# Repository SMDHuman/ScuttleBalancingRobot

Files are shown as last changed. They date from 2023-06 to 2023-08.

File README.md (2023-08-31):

# Scuttle Self-Balancing robot

This project of mine was built with the support of [SCUTTLE™](https://www.scuttlerobot.org/). 

## About The Project

This project's subject is to make SCUTTLE Robot balance itself on its two wheels only modifying its default shape and use external MPU6050 sensor in addition. Main idea of this project comes from David Malawey who is Founder of The Scuttle™ and I am glad to bring this idea to reality. Before working on this project i had one project similar to this and it's called [LOTP_BalanceWheel](https://github.com/SMDHuman/BalanceWheel) and its purpose is to make a 3D printed frame, stepper motor driven and Raspberry Pi Pico based two wheels self-balancing robot.

However I have built a two wheels self-balancing robot before, there were a few challenges on this project which I enjoyed a lot. Scuttle Robot has already a predefined setup and I was limited to transform current model in a most easiest and efficient way. Also a new part was designed and printed for this project to be able to hold MPU6050 sensor on the chassis.

Final result is a milestone and an evolutionary progress at SCUTTLE development for all community.
SCUTTLE Robot is designed very efficiently and maker friendly.  Standard form is a very good start for different purpose designs. It may be adapted for various potential tasks. There are still many challenges hidden at SCUTTLE Robot for curious makers. This project is a very good sample of that. I hope you enjoy while you are building your own.

## Requirements 

If you want to replicate this project on your own, you'll need;
1.	Raspberry Pi Computer,
2. [Scuttle Robot Base Parts](https://github.com/SMDHuman/ScuttleBalancingRobot/blob/main/docs/Item%20Links%2020230606.pdf),
3.	MPU6050
4.	Custom 3D Printed Parts,
5.	Basic Python Knowledge,
6.	Basic understanding of PID Controller (in case of re-tuning PID)

With all of those you can easily remake or iterate on top of it.

# Getting Started

First of all you need the robot itself to install and run the programs. If you have one, then you are lucky! You just need to transform the shape of the robot and attach external MPU6050 sensor and a [3D print part](https://github.com/SMDHuman/ScuttleBalancingRobot/tree/main/3D%20Models) to mount it. You can start this process by looking up my step by step [YouTube](https://youtu.be/XI1HBQYeNek) guide with English subtitle or check out the [PDF](https://github.com/SMDHuman/ScuttleBalancingRobot/blob/main/docs/Self%20Balanced%20Robot%20Transformation.pdf) of the transformation of the robot from base model to self-balancing configuration.

If you don't have the robot, then you can obtain all the parts from [Scuttle Shop](https://www.scuttlerobot.org/shop/) or from your local shops. You can look the parts and specification of those parts from this [PDF](https://github.com/SMDHuman/ScuttleBalancingRobot/blob/main/docs/Item%20Links%2020230606.pdf) or in that [Link](https://www.scuttlerobot.org/resources/). You will find lots of documentation about SCUTTLE Robot in this link too.

## Wiring of Necessary Components

You have to wire all electrical components to each other that are in use of our project. We need to wire
*	Batteries to Regulator,
*	Batteries to Motor driver,
*	Regulator to Raspberry Pi,
*	Raspberry Pi to Motor Drivers,
*	Motor Driver to DC Motors,
*	MPU6050 to Raspberry Pi.

You can check out the connections of all parts and more from this Link except MPU6050. MPU6050 needs to connect to Raspberry Pi as the picture shows under below.

Direct Connections with Raspberry Pi and MPU6050

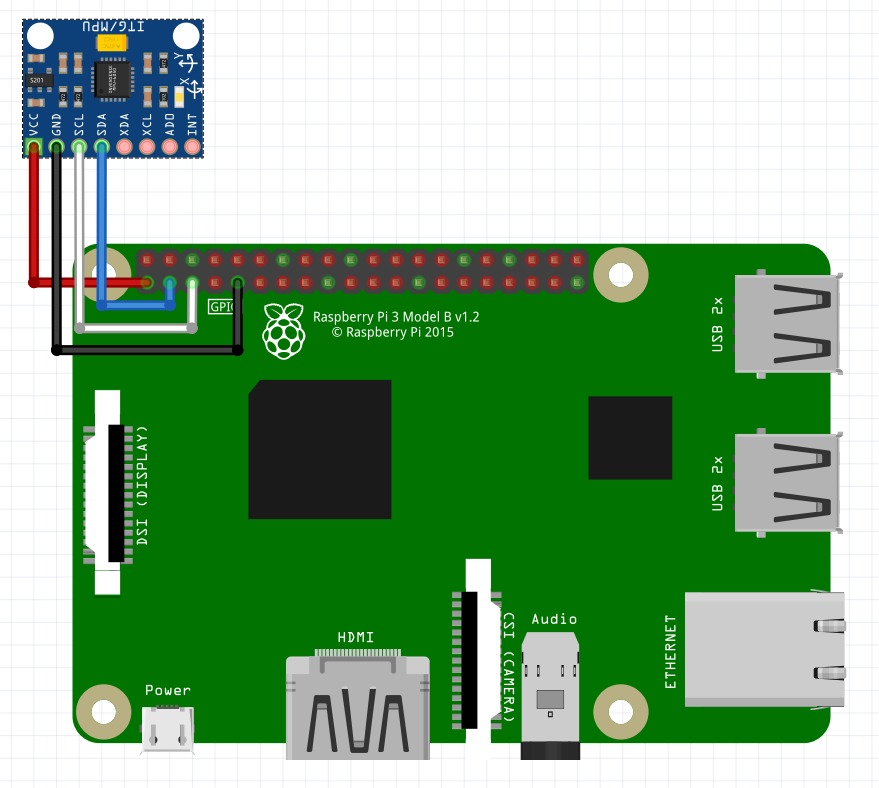
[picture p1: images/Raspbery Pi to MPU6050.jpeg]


Connection Via I2C Breakout Board

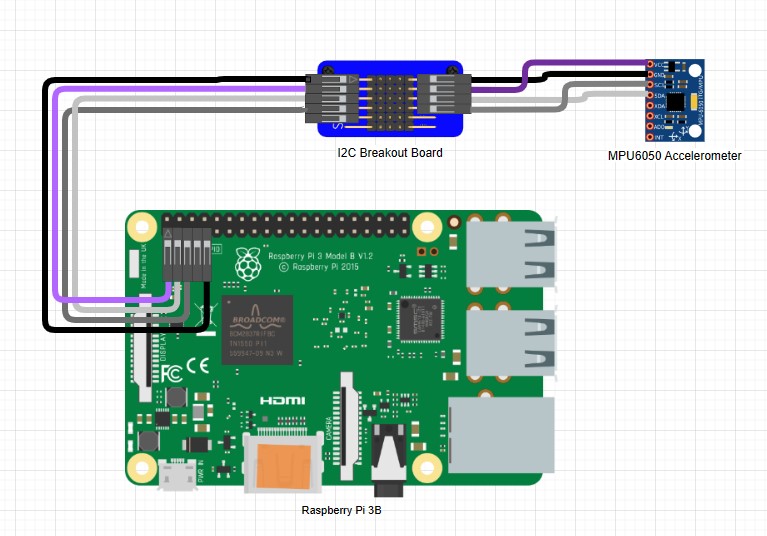
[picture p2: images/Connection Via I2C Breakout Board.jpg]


If you can't see the picture, here is a table of the wiring of the pins between MPU6050 and Raspberry Pi. You may also access the diagram designed on [Draw.io](https://drive.google.com/file/d/1K8wL2eJak03yuCxYKJeCcMRbwO4yd8io/view?usp=sharing)

| MPU6050 | Raspberry Pi |
|---|---|
| VCC | 3.3V |
| GND | GND |
| SCL | GPIO 3 |
| SDA | GPIO 2 |

## Installation 
You can follow the step by step guide from [this document](https://github.com/SMDHuman/ScuttleBalancingRobot/blob/main/docs/Software%20Installation%20Guide%20v1.pdf) prepeared for installation of OS and running the python code for self balancing scuttle robot.

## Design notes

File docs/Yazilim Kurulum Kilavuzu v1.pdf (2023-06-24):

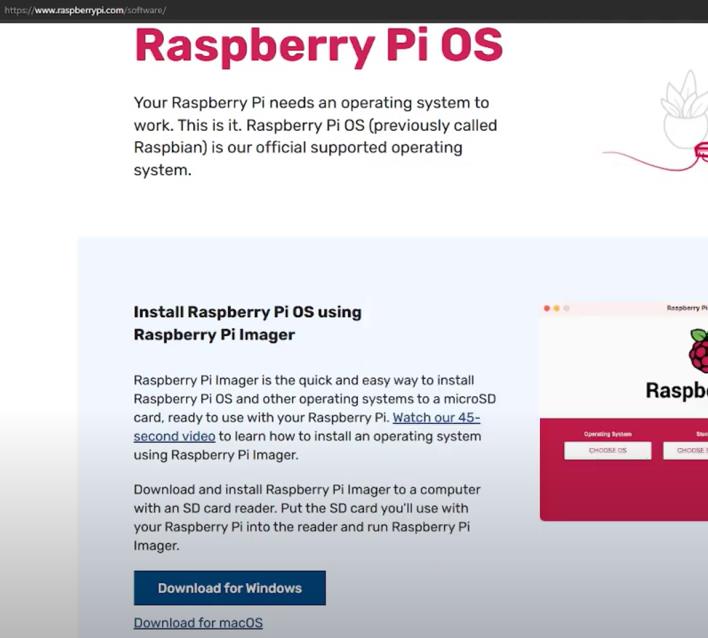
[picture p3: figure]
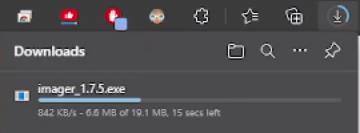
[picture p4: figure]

SCUTTLE Denge Robotu - Yazılım Kurulum Kılavuzu | Dok Ver. 1.0

Sayfa

1

## SCUTTLE Denge Robotu - Yazılım Kurulum Kılavuzu

### 1. Adım : Raspberry Pi’nin SD kartını Bilgisayarımıza takıyoruz

Minimum 4 GB bir SD kart yeterli olacaktır.

2. Adım : Rasberry Pi’nin web sitesinden Raspbian işletim sisteminin Lite versiyonunu indirip Raspberry Pi’nin SD kartına kurulumunu yapıyoruz, gerekli seçenekleri ve bilgileri giriyoruz.
a. İlk olarak Rasberry Pi’nin web sitesini açıyoruz ve “software”i seçiyoruz.

https://www.raspberrypi.com/software/

b. Bu bölümden Raspberry Pi Imager programını indiriyoruz.

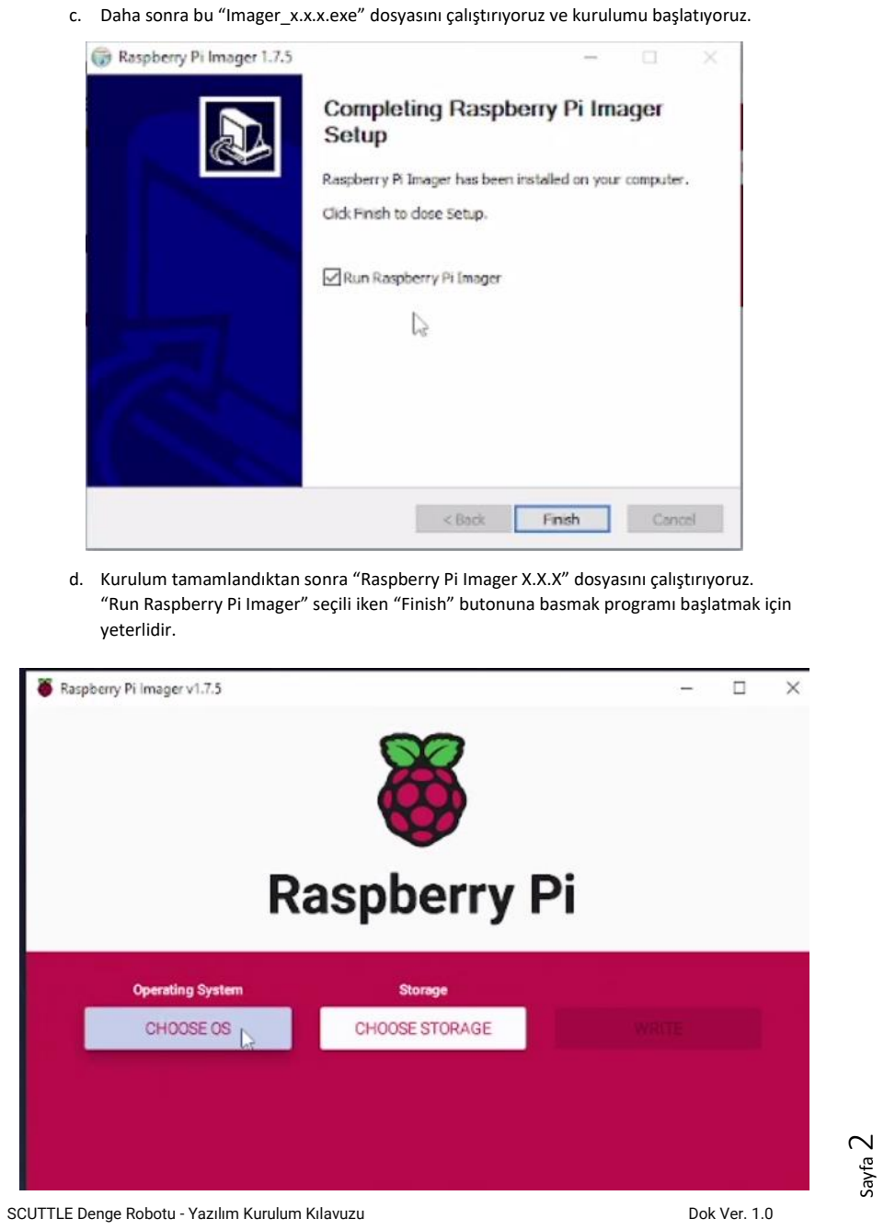
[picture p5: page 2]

Sayfa

2

c. Daha sonra bu “Imager_x.x.x.exe” dosyasını çalıştırıyoruz ve kurulumu başlatıyoruz.
d. Kurulum tamamlandıktan sonra “Raspberry Pi Imager X.X.X” dosyasını çalıştırıyoruz. “Run Raspberry Pi Imager” seçili iken “Finish” butonuna basmak programı başlatmak için yeterlidir.

Sayfa

3

e. İlk olarak “Choose OS” butonuna basarak işletim sistemini seçeceğimiz pencereyi açıyoruz. Burada önce “ Raspberry Pi OS (other)” seçeneğini seçiyoruz.
f. Daha sonra “Raspberry Pi OS Lite (32-bit)” işletim sistemini seçiyoruz. Siz dilerseniz “Raspberry Pi OS (32-bit)” işletim sistemini de seçebilirsiniz.
g. Ardından işletim sisteminin nereye kurulacağını seçmek için “Choose Storage” butonuna basıyoruz.
h. SD kartımızı seçiyoruz.

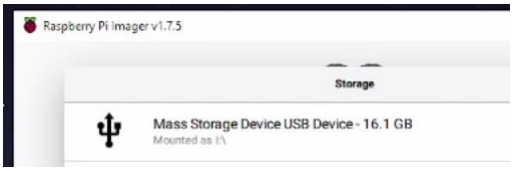
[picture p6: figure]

i. Diğer işleme geçiyoruz ve “Ayarlar” butonuna basıyoruz.
j. Açılan pencerede ilk olarak “image customization options” için “to always use” seçeneğini seçiyoruz. Böylece bu yaptığımız ayarları her seferinde yeniden yapmamıza gerek kalmıyor ve bu değişiklikler kalıcı şekilde sisteme kaydediliyor.

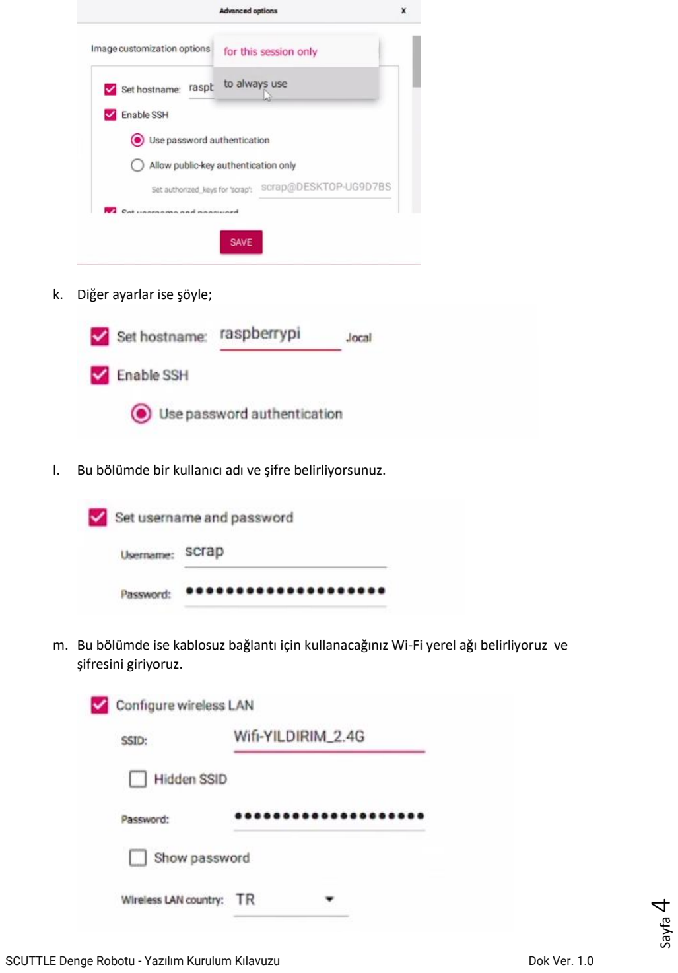
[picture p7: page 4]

Sayfa

4

k. Diğer ayarlar ise şöyle;
l. Bu bölümde bir kullanıcı adı ve şifre belirliyorsunuz.
m. Bu bölümde ise kablosuz bağlantı için kullanacağınız Wi-Fi yerel ağı belirliyoruz ve şifresini giriyoruz.

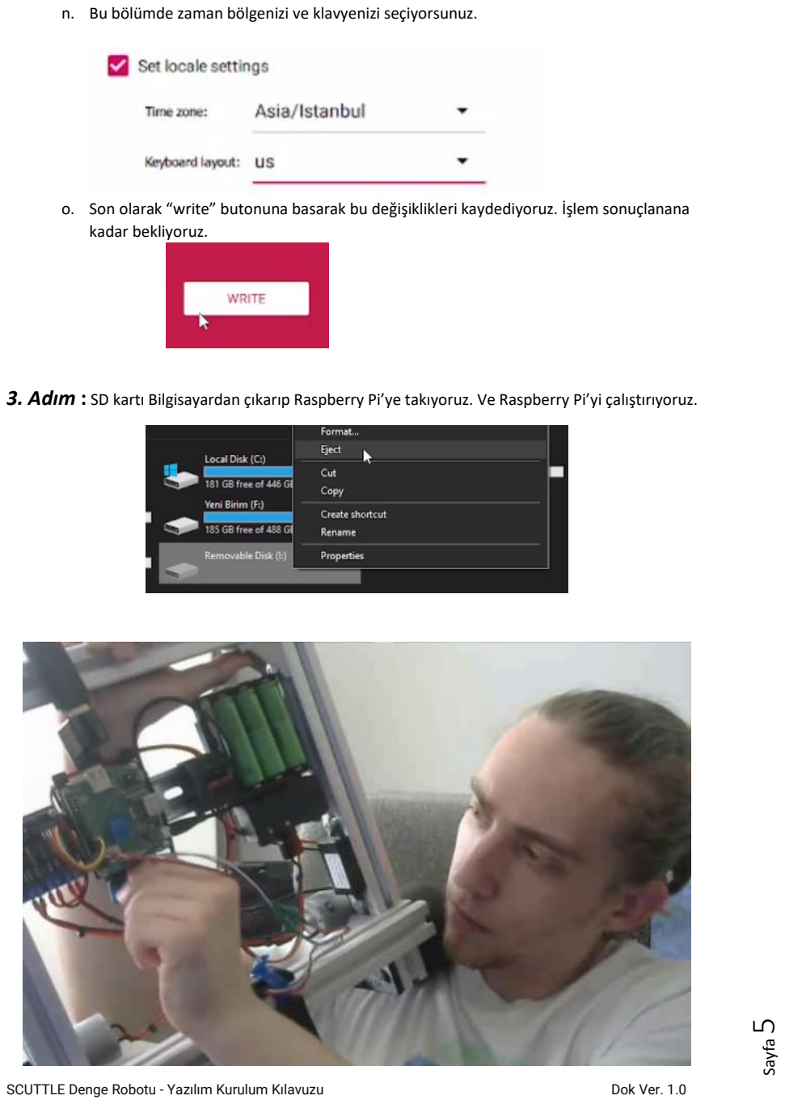
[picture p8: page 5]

Sayfa

5

n. Bu bölümde zaman bölgenizi ve klavyenizi seçiyorsunuz.
o. Son olarak “write” butonuna basarak bu değişiklikleri kaydediyoruz. İşlem sonuçlanana kadar bekliyoruz.
3. Adım : SD kartı Bilgisayardan çıkarıp Raspberry Pi’ye takıyoruz. Ve Raspberry Pi’yi çalıştırıyoruz.

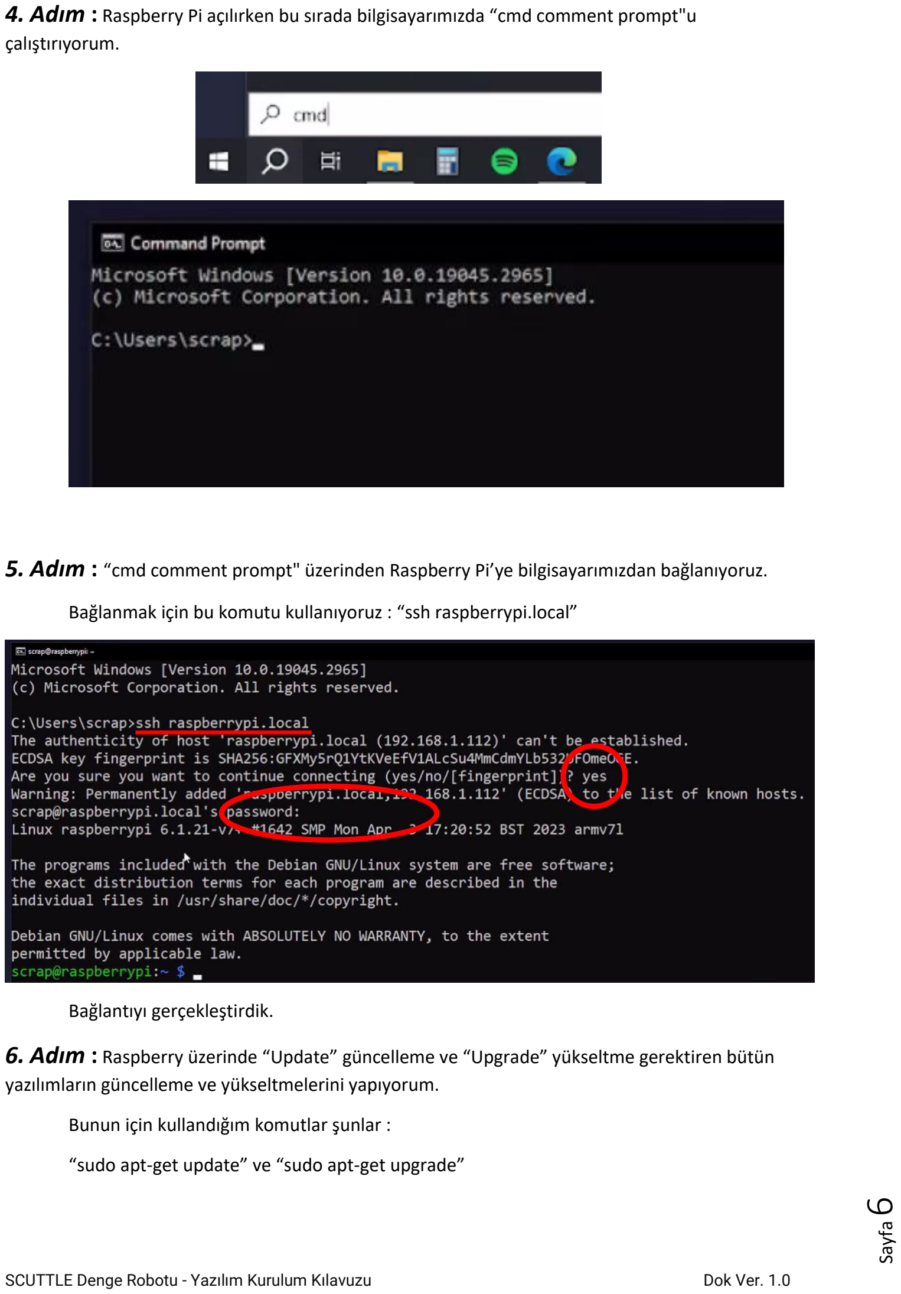
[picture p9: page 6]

Sayfa

6

### 4. Adım : Raspberry Pi açılırken bu sırada bilgisayarımızda “cmd comment prompt"u

çalıştırıyorum.

5. Adım : “cmd comment prompt" üzerinden Raspberry Pi’ye bilgisayarımızdan bağlanıyoruz.

Bağlanmak için bu komutu kullanıyoruz : “ssh raspberrypi.local”

Bağlantıyı gerçekleştirdik.

### 6. Adım : Raspberry üzerinde “Update” güncelleme ve “Upgrade” yükseltme gerektiren bütün

yazılımların güncelleme ve yükseltmelerini yapıyorum.

Bunun için kullandığım komutlar şunlar :

“sudo apt-get update” ve “sudo apt-get upgrade”

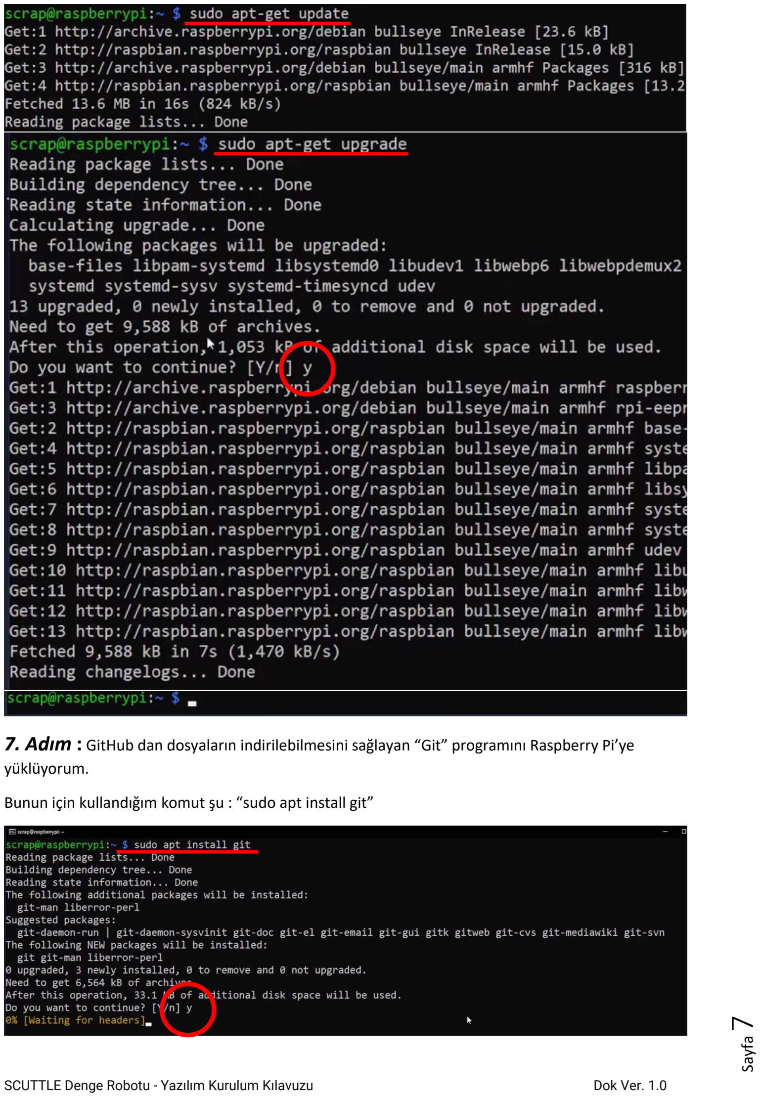
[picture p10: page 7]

Sayfa

7

7. Adım : GitHub dan dosyaların indirilebilmesini sağlayan “Git” programını Raspberry Pi’ye yüklüyorum.

Bunun için kullandığım komut şu : “sudo apt install git”

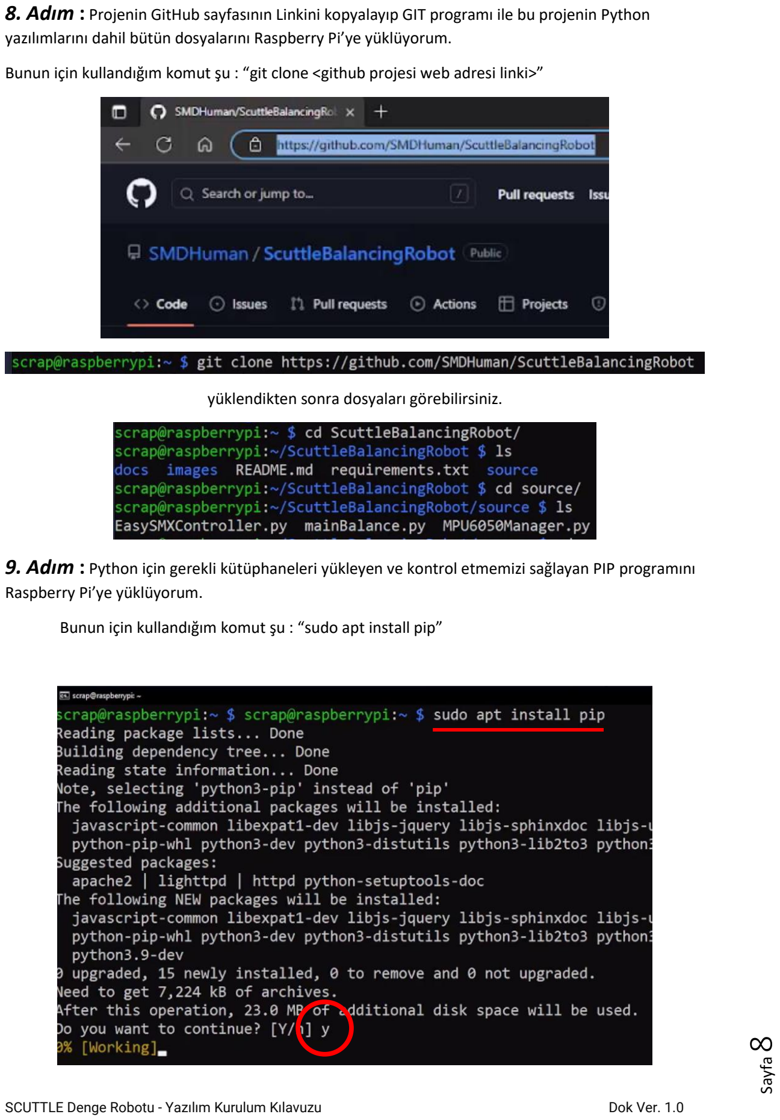
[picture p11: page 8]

Sayfa

8

8. Adım : Projenin GitHub sayfasının Linkini kopyalayıp GIT programı ile bu projenin Python yazılımlarını dahil bütün dosyalarını Raspberry Pi’ye yüklüyorum.

Bunun için kullandığım komut şu : “git clone <github projesi web adresi linki>”

yüklendikten sonra dosyaları görebilirsiniz.

9. Adım : Python için gerekli kütüphaneleri yükleyen ve kontrol etmemizi sağlayan PIP programını Raspberry Pi’ye yüklüyorum.

Bunun için kullandığım komut şu : “sudo apt install pip”

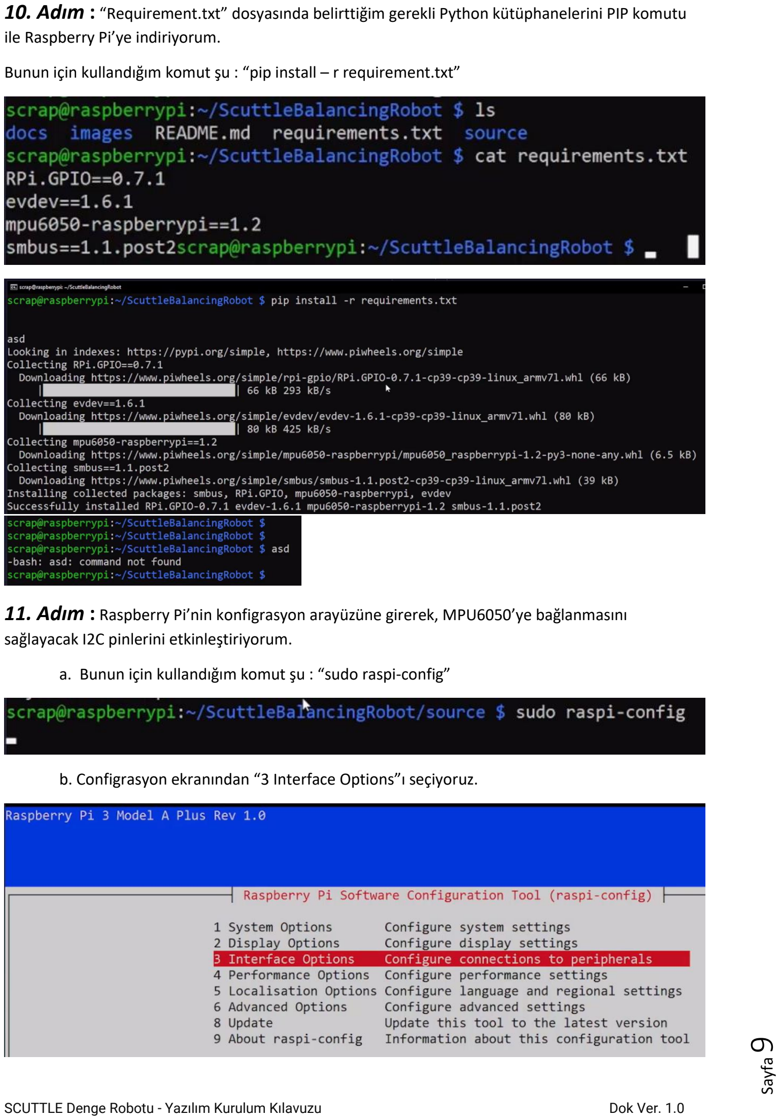
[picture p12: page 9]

Sayfa

9

10. Adım : “Requirement.txt” dosyasında belirttiğim gerekli Python kütüphanelerini PIP komutu ile Raspberry Pi’ye indiriyorum.

Bunun için kullandığım komut şu : “pip install – r requirement.txt”

### 11. Adım : Raspberry Pi’nin konfigrasyon arayüzüne girerek, MPU6050’ye bağlanmasını

sağlayacak I2C pinlerini etkinleştiriyorum.

a. Bunun için kullandığım komut şu : “sudo raspi-config”
b. Configrasyon ekranından “3 Interface Options”ı seçiyoruz.

# Sayfa 10

c. Burada “I5 I2C Enable/disable”ı seçiyoruz.

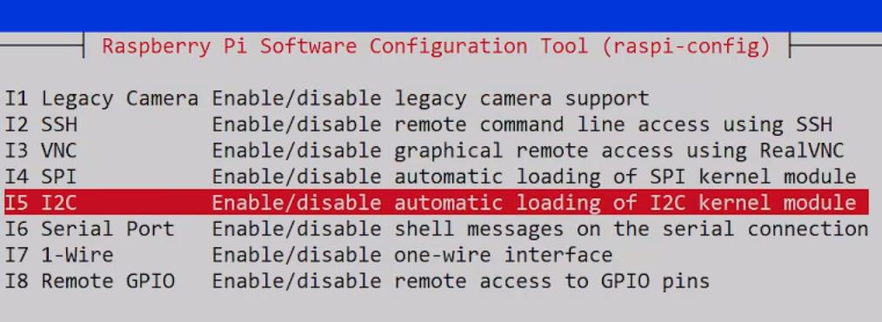
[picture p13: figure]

d. “ARM I2C arayüzü”nü etkinleştirmek için “Yes” tuşuna basıyorum.

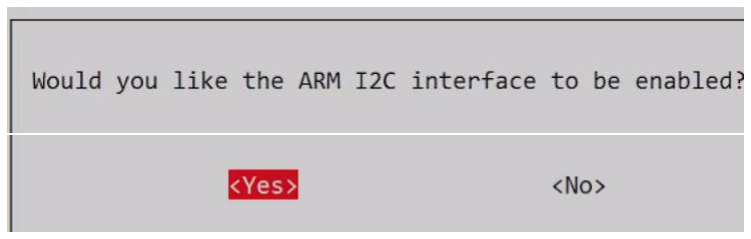
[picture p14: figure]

e. “ARM I2C” etkinleştirildi.

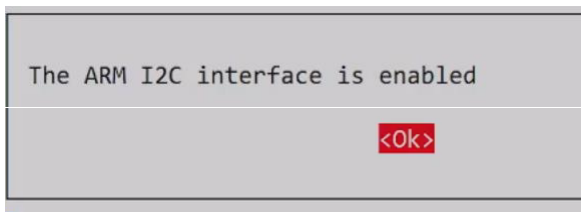
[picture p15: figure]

12. Adım : “mainBalance.py” Pyton yazılım dosyasını çalıştırıyorum. Ve Denge Programı çalışmaya başlıyor. Bunun için kullandığım komut şu : “python mainBalance.py”
13. Adım : Problem 1 : Kumanda ile iletişim kurmamızı sağlayan “Dongle” takılı olmadığında oluşacak problemin çözümünü burada anlatıyorum. Kumanda hangi isim ile Raspberry Pi tarafından tanınırsa bu ismin kod içinden güncellemesinin nasıl yapıldığını burada anlatıyorum.
a. İlk olarak “Dongle”ı robotumdan çıkarıyorum.
b. “nano mainBalance.py” komutunu vererek “mainBalance.py” dosyasını açıyoruz.

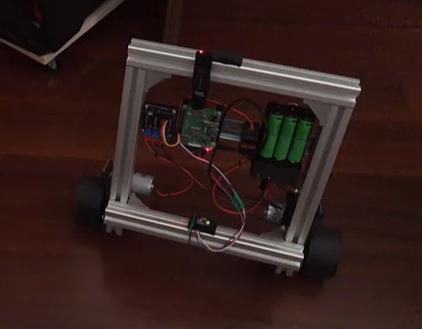
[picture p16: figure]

# Sayfa 11

c. Burada Controller “event0” olarak görülmektedir.

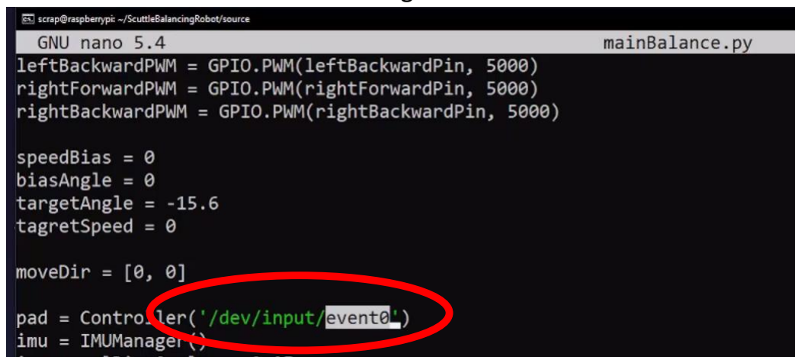
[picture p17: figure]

d. “ls /dev/input” komutu ile sadece “event0” görülebiliyor.
e. “Dongle” tekrar Raspberry Pi’ye takıyorum.
f. “ls /dev/input” komutu ile artık baktığımızda “event1” olarak yeni kontrol kumandası sisteme eklendiğini görebiliriz.
g. “mainBalance.py” dosyasında bu satır bu şekilde düzeltildiğinde Kontrol Kumandasının sistem tarafından görülmesi sağlanır. “pad = Controller (‘/dev/input/event1’)”
14. Adım : Robotum sorunsuz çalışıyor.

# Sayfa 12

### 15. Adım : Problem 2 : Kumanda markası ile ilgi sorun yaşanması durumunda hangi yazılım

dosyasının düzenlenmesi gerektiğini burada anlatıyorum.

“EasySMXController.py” dosyasından gerekli düzenlemeler yapılır ve Yeni farklı marka kumanda sisteme tanıtılabilir.

16. Adım : Kumandayı devre dışı bırakmak isterseniz kod içinde yapılması gereken değişiklikler bunlardır..
a. İlk olarak . “nano mainBalance.py” komutunu ile “mainBalance.py” dosyasını açıyoruz.

b.” from EasySMXConroller import Controller” satırının başına “#” koyuyorum, satırı devre dışı bırakmak için

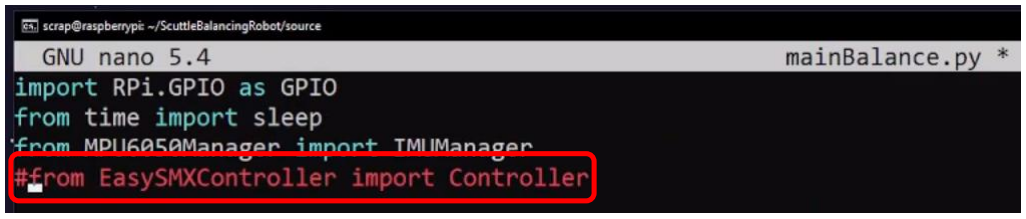
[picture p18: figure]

c.”pad= Conroller(‘/dev/input/event1’)‘” satırının başına “#” koyuyorum, satırı devre dışı bırakmak için

d. “speedPID.target” ve “moveDir[1]” değişkenlerine 0 atıyorum
17. Adım : Robotumuzun sabit bir hızda gitmesini yada sabit yerinde kalmasını, aşağıdaki şekilde kod içinde yapacağımız değişiklerle sağlayabiliriz.

“speedPID.target” robotun hızını kontrol ettiğim bir değişken. Bu değişkene 0 değeri atarsam robot yerinde sabit durur ve hareket etmez.

18. Adım : Robotun ne kadar sağa yada ne kadar sola döneceğini, yada dönmeden sabit kalmasını kod içinde yapacağımız şu değişikliklerle sağlıyoruz

# Sayfa 13

“speedPID.target” robotun sağa sola dönüşlerini kontrol ettiğim bir değişken. Bu değişkene 0 değeri atarsam robot yerinde sabit durur ve sağa sola dönmez.

19. Adım : PID ince ayarlarını kod üzerinde aşağıdaki şekilde yapabiliriz.

PID değerlerine ince ayar gerektiğinde p,i,d ve sp,si,sd değişkenlerinin değerlerini değiştirerek en başarılı değerleri bulabilirsiniz.

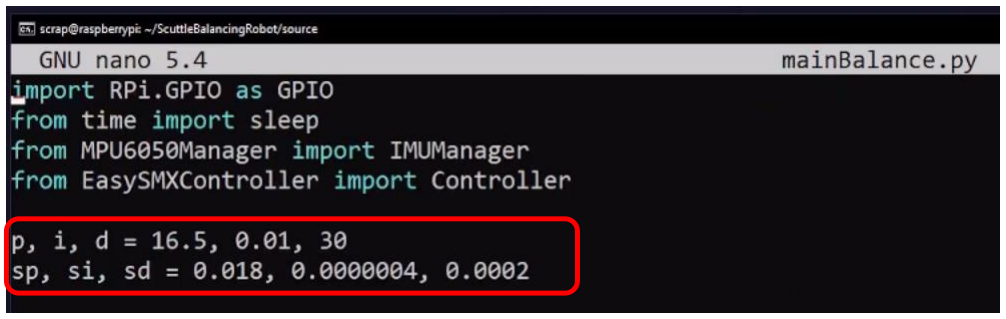
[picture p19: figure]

### 20. Adım : Tebrikler. Artık SCUTTLE robotunuzun iki teker üzerinde dengede kalmasını

sağlayabilirsiniz. Sizlerden gelen öneriler ile bu dokümanı güncel tutmak istiyorum. Lütfen gördüğünüz eksiklikleri ya da geliştirilmesi gereken yerleri reductalimenitis@gmail.com mail adresime gönderin, mutlaka üzerlerinde çalışacağım. İyi eğlenceler.

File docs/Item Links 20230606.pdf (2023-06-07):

Store | Part | PN | qty needed | Link from TURKEY | PN
amazon | Wheel, urethane 83mm, with bearings (pair) | B07531B4GK | 1 | https://www.amazon.com.tr/Elektrikli-Scooter-Tekerlekleri-Longboard-Lastikleri/dp/B0C5W5FQ6N | B0C5W5FQ6N
| | | | https://www.trendyol.com/prc/608-zz-rulman-8x22x7-10-adet-p-84773487 | or
| | | | https://www.amazon.com.tr/608ZZ-Rulmanlar%C4%B1-Ya%C4%9Flanm%C4%B1%C5%9F-Performans-Rulmanlar/dp/B07JJ1SKL4 | B07JJ1SKL4
| Corner bracket caps | | 4
amazon | Bracket - 90deg aluminum, for 3030 (for chassis) | B07BQR7WX8 | 4 | https://www.amazon.com.tr/sabitleme-malzemesi-VORXEON-3030-al%C3%BCminyum/dp/B0BHW7SMZ5 | B0BHW7SMZ5
Mcmaster | Timing Belt, 5mm pitch, 245mm length, 9mm width | B08PW2HD81 | 2
Mcmaster | Hex Nut, M8 (for axle) | 90591A161 | 2 | https://www.n11.com/urun/somun-m8-8li-paket-29046478
Mcmaster | T-slot Framing Extrusion - 30mm x 1ft (for chassis) | 5537T97 | 4 | https://www.urhanshop.com/machifit-300mm-uzunluk-3030-t-slot-aluminyum-profiller-cnc-icin-ekstruzyon-cercevesi-u86308
amazon | Caster wheels (for front) | B01J4FED5E | 2 | https://www.tekerteker.com/zet-4lu-tablali-tpe-doner-tekerlek-50-mm-cap
Mcmaster | Screws - M8x110mm screw (axles) | 91290A470 | 2 | https://www.hirdavatim.com.tr/urun/m8-imbus-civatalar-8-8-kalite-din-912-110-mm-m8 | or
| M8 hex nut | | 2 | https://www.amazon.com.tr/C%C4%B1vatalar%C4%B1-Alt%C4%B1gen-Somunlar-Tahrikli-Kaplama/dp/B08J2KFG5D | B08J2KFG5D
Mcmaster | Screws - M6 x 10mm (for casters & chassis brackets) | 91239A316 | 23 | https://www.amazon.com.tr/Paslanmaz-%C3%87elik-Alt%C4%B1gen-Soket-Yuvarlak/dp/B08M5NS8XR | B08M5NS8XR
Mcmaster | Screw, Flat head, M3x10mm (for motors 6) | 92010A120 | 6 | https://www.n11.com/urun/m3-x-10mm-duz-basli-plastik-civata-vida-siyah-x-5-adet-3481412
amazon | Screw, self-tapping, M2 x 6mm, for plastic (for encdr brkt 4, ultrsnc brkt 4) | B00GMQDSRI | 5 | https://www.trendyol.com/sywoods/100-adet-6-5-mm-mini-hobi-vidasi-siyah-p-270315909 | or
| | | | https://www.amazon.com.tr/XFentech-Adet-M1-7-Kendinden-Kesen/dp/B08RRWBH8C | B08RRWBH8C
Mcmaster | Screw, M2.5x10mm countersunk (for battery case) | 92010A020 | 4 | https://www.ayazbaglanti.com/ayaz-m2.5x10-paslanmaz-inox-yhb-vida-din965-a2-70-304-kalite-27iyhb2510 | or
| | | | https://www.amazon.com.tr/Ba%C5%9Fl%C4%B1-B%C3%BCy%C3%BCk-%C3%87apraz-K%C3%BC%C3%A7%C3%BCk-M2-M4-M2-555200/dp/B096DD3RPQ | B096DD3RPQ
Mcmaster | Screw, M2.5x6mm pan head (for motor driver mount 2, bbb lid 1) | 92005A066 | 11 | https://www.n11.com/urun/m25x6-ysb-yildiz-silindir-bas-vida-100-adet-7224423
amazon | Slide-in Nut, M6 nickel-plated steel for 3030 T-slot extrusion | B077Z2HX42 | 23 | https://www.amazon.com.tr/EYPINS-s%C3%BCrg%C3%BCl%C3%BC-al%C3%BCminyum-ekstr%C3%BCzyon-projeleri/dp/B09P2XCCSY | B09P2XCCSY
Mcmaster | Washer, flat washer for M8 Bolt (for axles) | 93475A270 | 4 | https://www.pazarama.com/m8-genis-pul-350-adet-p-2067792714427
Mcmaster | Washer, M6x12mm, flat washer (wheelBrackets) | 93475A250 | 6 | https://www.pazarama.com/m6-pul-350-adet-p-5599513355576
Mcmaster | Washer, M6, split lock (for casters) | 91202A234 | 6 | https://www.n11.com/urun/m6-rondela-yayli-pul-80-adet-7225825
Amazon | 305mm dinrail | B08J8DVPGG | 1 | https://www.amazon.com.tr/Taiss-Kaliteli-Da%C4%9F%C4%B1t%C4%B1m-Geni%C5%9Flik-Y%C3%BCkseklik/dp/B08CKKBP5N | B08CKKBP5N
Mcmaster | Threaded insert, M2.5 x 3.4 heat set (btry 2, whlplts 4, m.driver 2) | 94180A321 | 5 | https://www.makertechstore.com/products/copy-of-heat-set-threaded-inserts-m2-5-threads?variant=29739547852897 | ?
| | | | https://shop4fasteners.co.uk/heat-ultrasonic-threaded-inserts-brass-m2-5-x-5-74mm.html | ?
| | | | https://www.amazon.com.tr/di%C5%9Fli-pirin%C3%A7-t%C4%B1rt%C4%B1ll%C4%B1-a%C4%9Fa%C3%A7-yuvas%C4%B1/dp/B07SYP6PRJ | B07SYP6PRJ
mouser | Raspberry Pi 4, 2gb RAM | 713-102991317 | 1 | https://www.amazon.com.tr/Raspberry-bilgisayar-ARM-Cortex-A72-Bluetooth-Micro-HDMI/dp/B07TD42S27 | B07TD42S27
amazon | Motor Driver Board with Twin MC33886 H-Bridges (HW-231 model) | B07VHFCYFQ | 1 | https://robiz.net/dualmc33886 | or
| | | | https://www.hepsiburada.com/motorobit-mc33886-motor-surucu-karti-pm-HB00000SI5GW
amazon | Motor, DC 12v with 200 rpm gearbox (for drivetrain) | B072R5QSRG | 2 | https://www.milcad.net/urun/12v-200rpm-reduktorlu-dc-motor/ | or
| | | | https://www.robiduck.com/urun/12v-200rpm-37mm-reduktorlu-dc-motor
amazon | Camera, USB, 2.1mm focal len, 150 deg FOV | B07QSTPGR8 | 1 | https://www.robotistan.com/rpi-camera-m-fisheye-lens-1 | ?
amazon | Battery cell, Panasonic 18650 or other brand | B00GS48XRE | 3 | https://www.amazon.com.tr/Panasonic-NCR18650B-3400mAh-Li-ion-Edilebilir/dp/B0BNVXPQ2G | B0BNVXPQ2G
mouser | Encoder, AMS5048B, circuit boards | 990600491 | 2 | https://www.e-komponent.com/as5047d-series-magnetic-rotary-position-sensor-evaluation-board | ?
powerwerx | Anderson PowerPole Connectors, 30amp | WP30-100 | 8 | https://www.fruugo.com.tr/anderson-powerpole-600v-guc-arac%C4%B1-icin-20x-30a-elektrik-konektoru/p-168667830-360222371
digikey | Battery Tray, 3 cell li-ion (BK-18650-PC6 on digikey) | BK-18650-PC6 | 1 | https://robiz.net/lbb3dcplug
mouser | Switch, rocker, SPST 10A BLK ON-OFF Symbols (for battery case) | SRB22A2FBBNN | 1 | https://www.roboshop.com.tr/mini-on-off-power-switch-anahtar-2p-siyah-15x10
amazon | Terminals - 22-16 AWG Insulated Female Quick Connect Terminal | B06XCWFTJ9 | 2 | https://www.amazon.com.tr/Heschen-Ba%C4%9Flant%C4%B1l%C4%B1-Tamamen-Yal%C4%B1t%C4%B1ml%C4%B1-Terminali/dp/B07BPMRWLY | B07BPMRWLY
amazon | Power Wire - 18 AWG (black/red pair), price listed per meter | B07428NBCW | 1 | https://www.roboshop.com.tr/16-awg-rc-yumusak-silikon-kablo-16awg-lipo-batarya-kablosu-kirmizi
amazon | Cable, 20cm ribbon, with female Dupont terminals (i2c board ►encoders) | B07GCY6CH7 | 2 | https://www.amazon.com.tr/40-Pin-20cm-Di%C5%9Fi-Dupont/dp/B092TD6QHD | B092TD6QHD
| Motor driver signal wire | | 1 | https://www.n11.com/urun/4-pin-bant-flat-kablo-022-mm-3320345
amazon | Cable, 10cm ribbon, with female Dupont terminals (pi►motor driver) | B07GD312VG | 1 | https://www.amazon.com.tr/40-Adet-Di%C5%9Fi-Di%C5%9Fi-Jumper-Kablo/dp/B09QJ6MSG3 | B09QJ6MSG3
amazon | battery management system (BMS) circuit board, 3S, 40A | B07JMY631D | 1 | https://www.amazon.com.tr/12-6V-18650-Lityum-Koruma-Mod%C3%BCl%C3%BC/dp/B09SDFRVN3 | B09SDFRVN3
amazon | battery cell charger, 18650 | B08DNQXB1C | 1 | https://www.amazon.com.tr/XTAR-Ak%C4%B1ll%C4%B1-Cihaz%C4%B1-Lityum-%C4%B0yon-Bataryalar/dp/B083S8HS4F | B083S8HS4F

mechanical

electronics

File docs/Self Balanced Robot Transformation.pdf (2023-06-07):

1. Start with Standard Setup

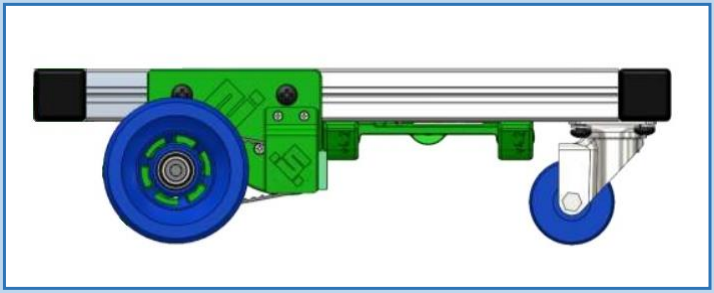
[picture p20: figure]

2. Remove Caster Wheels

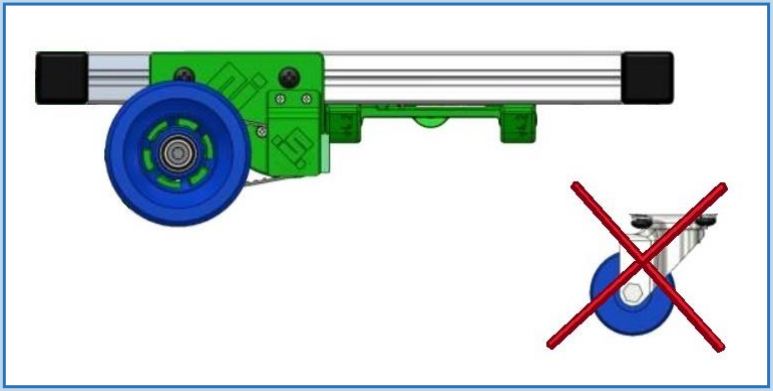
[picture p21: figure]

3. Remove Framing Rail

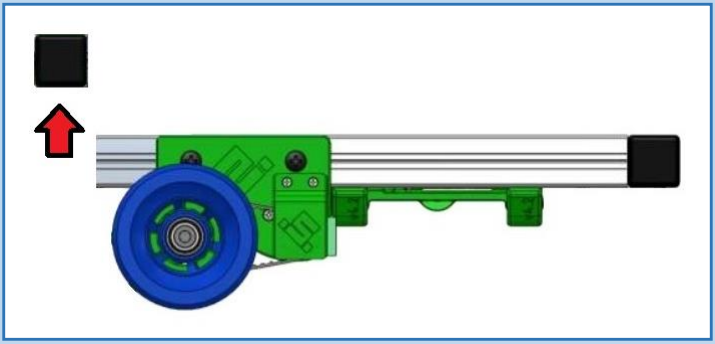
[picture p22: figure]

4. Move Wheels & Parts till End

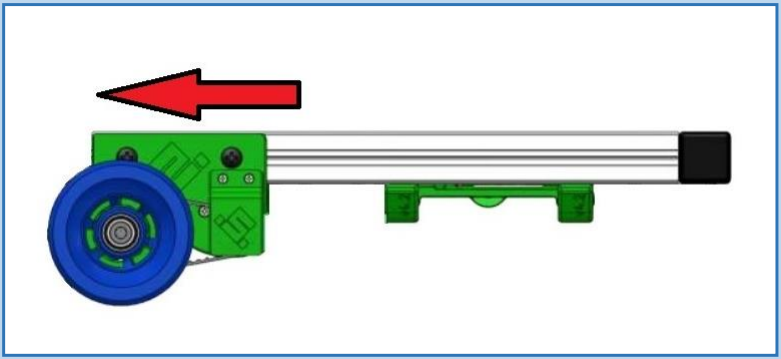
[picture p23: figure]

5. Mount the Framing Rail
Removed Before

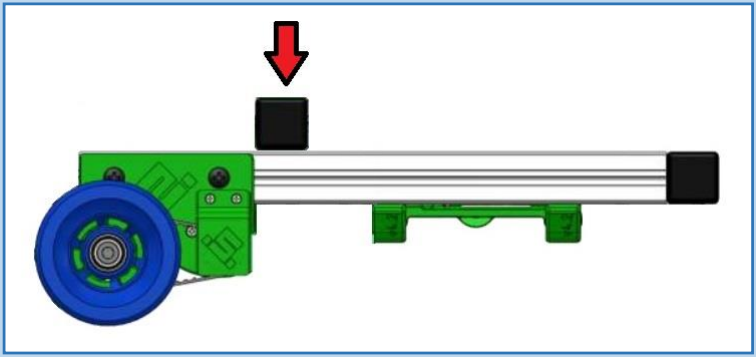
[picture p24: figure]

6. Mount MPU6050 Accelerometer and Gyroscope Sensor with 3D Printed Part Holder

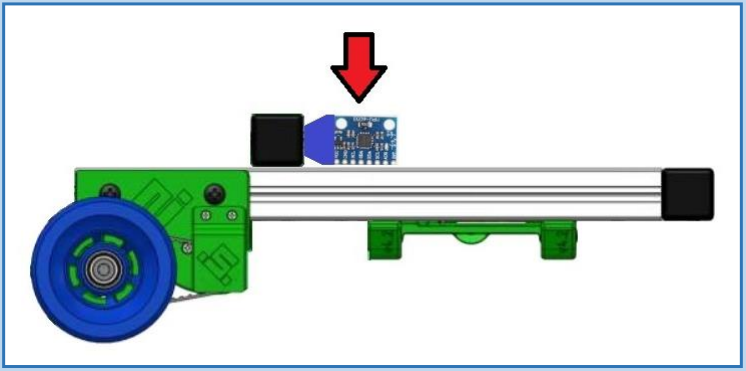
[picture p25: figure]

7. Connect Cables between MPU6050 and Raspberry PI

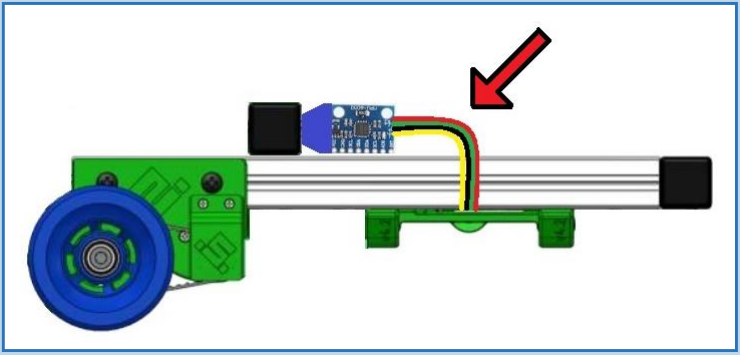
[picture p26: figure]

8. Download “Self-Balanced Robot” Software to Raspberry PI


9. Turn on Scuttle Robot and Let It Stand on 2 Wheels


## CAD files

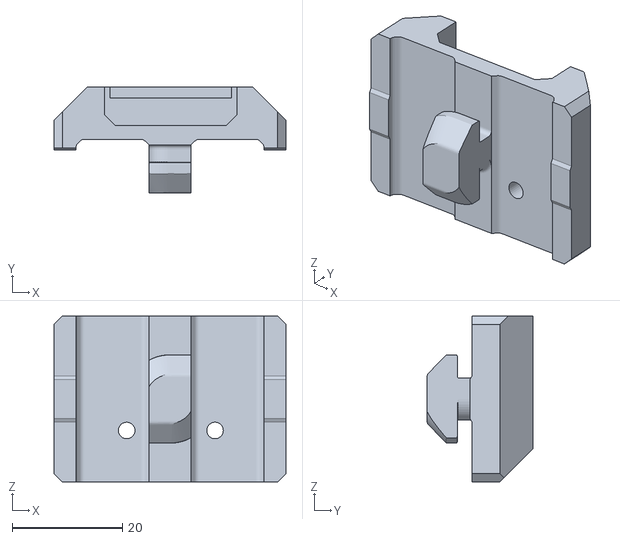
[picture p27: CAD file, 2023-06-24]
3D Models/Scuttle MPU6050 Mount.stl
42.0 x 19.2 x 30.0

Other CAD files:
3D Models/MPU_6050 Model.f3d
3D Models/Scuttle MPU6050 Mount.f3z

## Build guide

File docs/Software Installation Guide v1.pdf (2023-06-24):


SCUTTLE Self Balancing Robot - Software Installation Guide | Doc Ver. 1.0

Page

1

## SCUTTLE Self Balancing Robot - Software Installation Guide

Step 1: we will insert the Raspberry Pi's SD card into our Computer.

An SD card of at least 4 GB will be sufficient.

Step 2: we are downloading the Lite version of the Raspbian keyboard system on Rasberry Pi's web pages, installing the Raspberry Pi on the SD card, entering the necessary options and information.
a. First, we open the Rasberry Pi's website and select "software".

https://www.raspberrypi.com/software/

b. From this section, we download the Raspberry Pi Imager program.

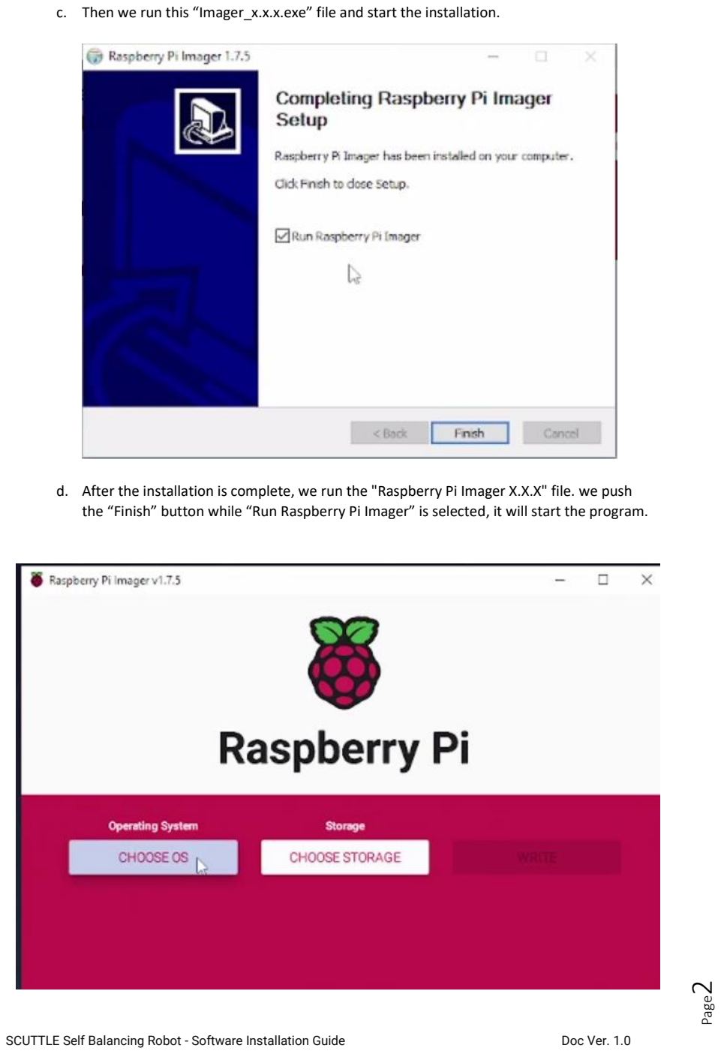
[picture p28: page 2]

Page

2

c. Then we run this “Imager_x.x.x.exe” file and start the installation.
d. After the installation is complete, we run the "Raspberry Pi Imager X.X.X" file. we push the “Finish” button while “Run Raspberry Pi Imager” is selected, it will start the program.

Page

3

e. First, we open the window where we will select the operating system by pressing the "Choose OS" button. Here we first select the “Raspberry Pi OS (other)” option.
f. Then we choose the operating system "Raspberry Pi OS Lite (32-bit)". You can also choose the “Raspberry Pi OS (32-bit)” operating system if you wish.
g. Then we press the "Choose Storage" button to choose where the operating system will be installed.
h. We select our SD card.

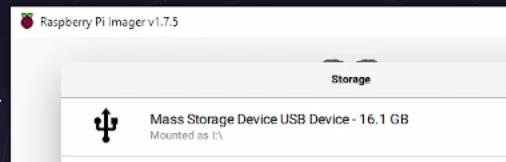
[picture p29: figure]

i. We go to the next process and press the "Settings" button.
j. In the window that opens, we first select the "to always use" option for "image customization options". Thus, we do not need to re-make these settings every time and these changes are saved to the system permanently.

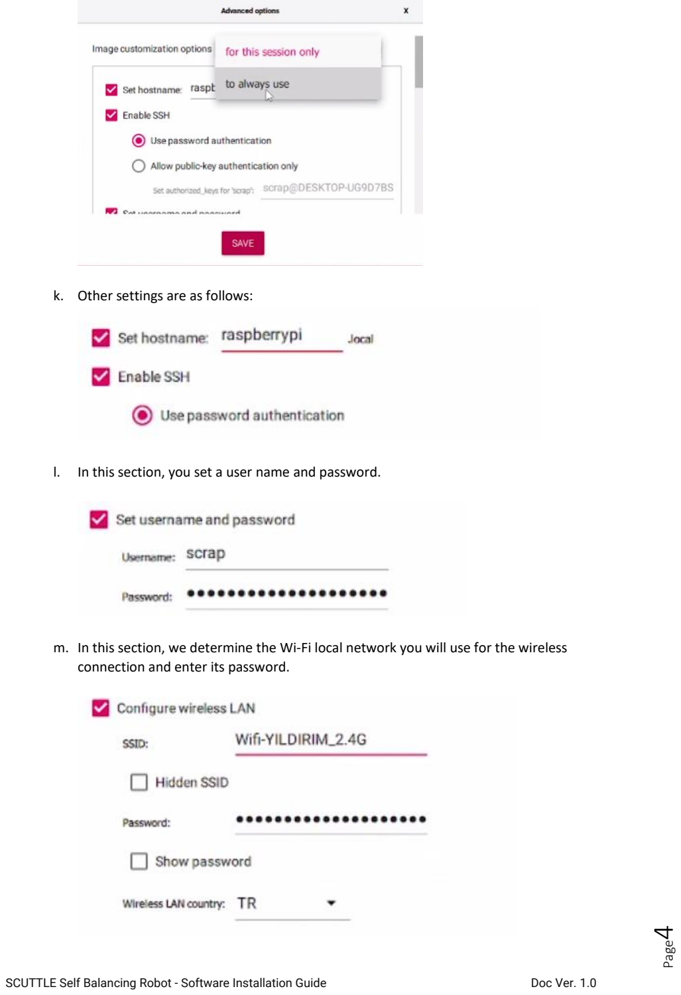
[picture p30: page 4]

Page

4

k. Other settings are as follows:
l. In this section, you set a user name and password.
m. In this section, we determine the Wi-Fi local network you will use for the wireless connection and enter its password.

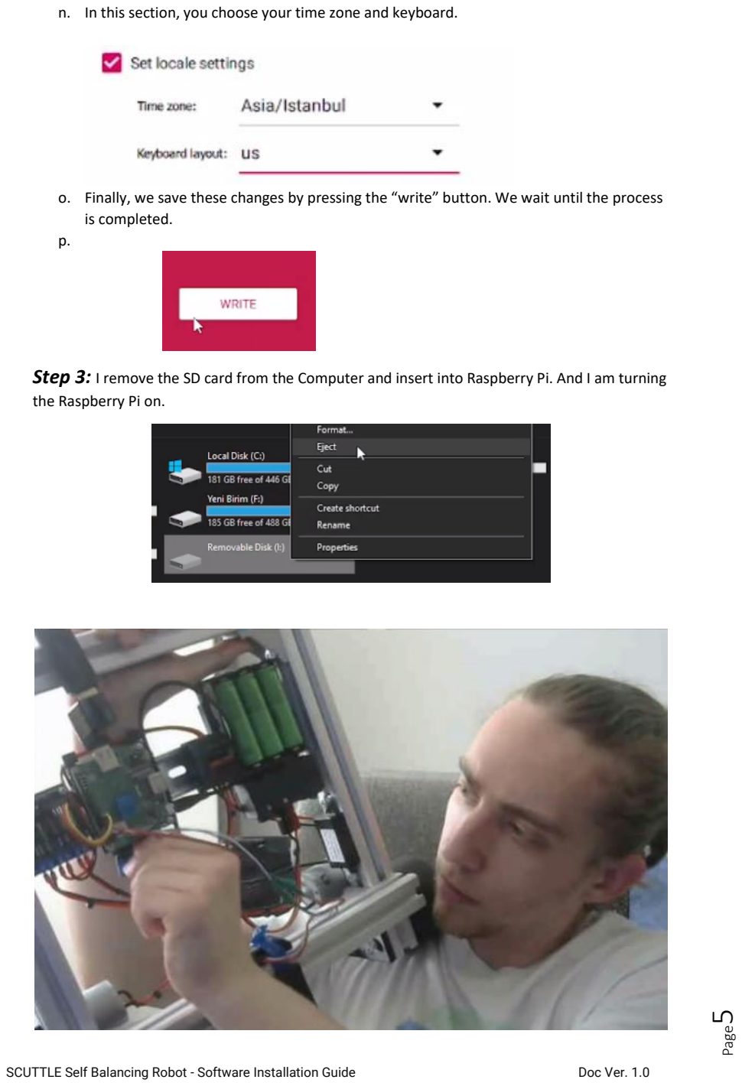
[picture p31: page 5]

Page

5

n. In this section, you choose your time zone and keyboard.
o. Finally, we save these changes by pressing the “write” button. We wait until the process is completed.
p.
Step 3: I remove the SD card from the Computer and insert into Raspberry Pi. And I am turning the Raspberry Pi on.

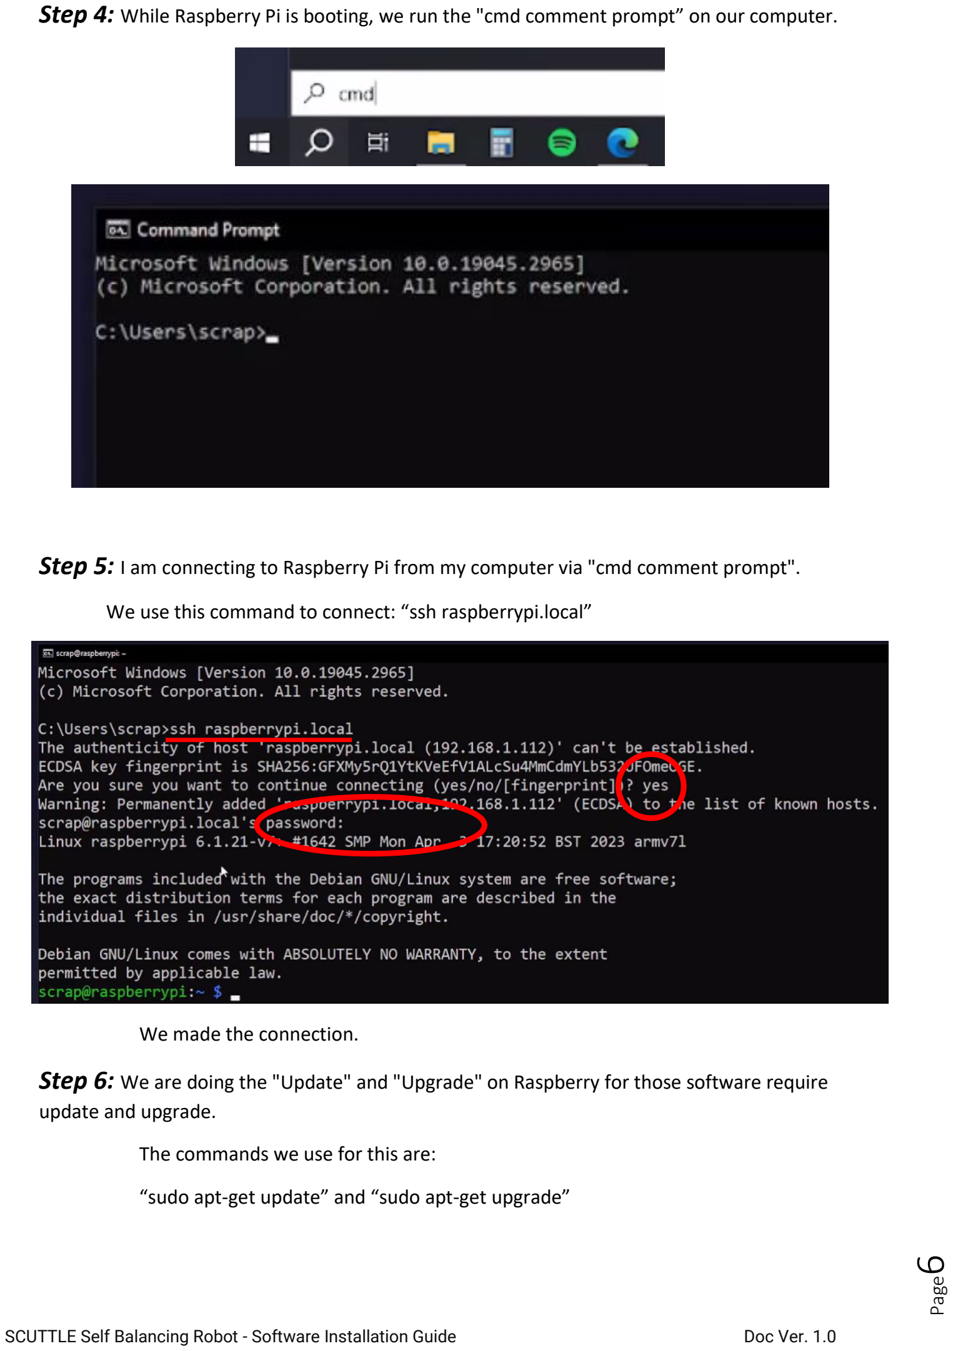
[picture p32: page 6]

Page

6

Step 4: While Raspberry Pi is booting, we run the "cmd comment prompt” on our computer.
Step 5: I am connecting to Raspberry Pi from my computer via "cmd comment prompt".

We use this command to connect: “ssh raspberrypi.local”

We made the connection.

Step 6: We are doing the "Update" and "Upgrade" on Raspberry for those software require update and upgrade.

The commands we use for this are:

“sudo apt-get update” and “sudo apt-get upgrade”

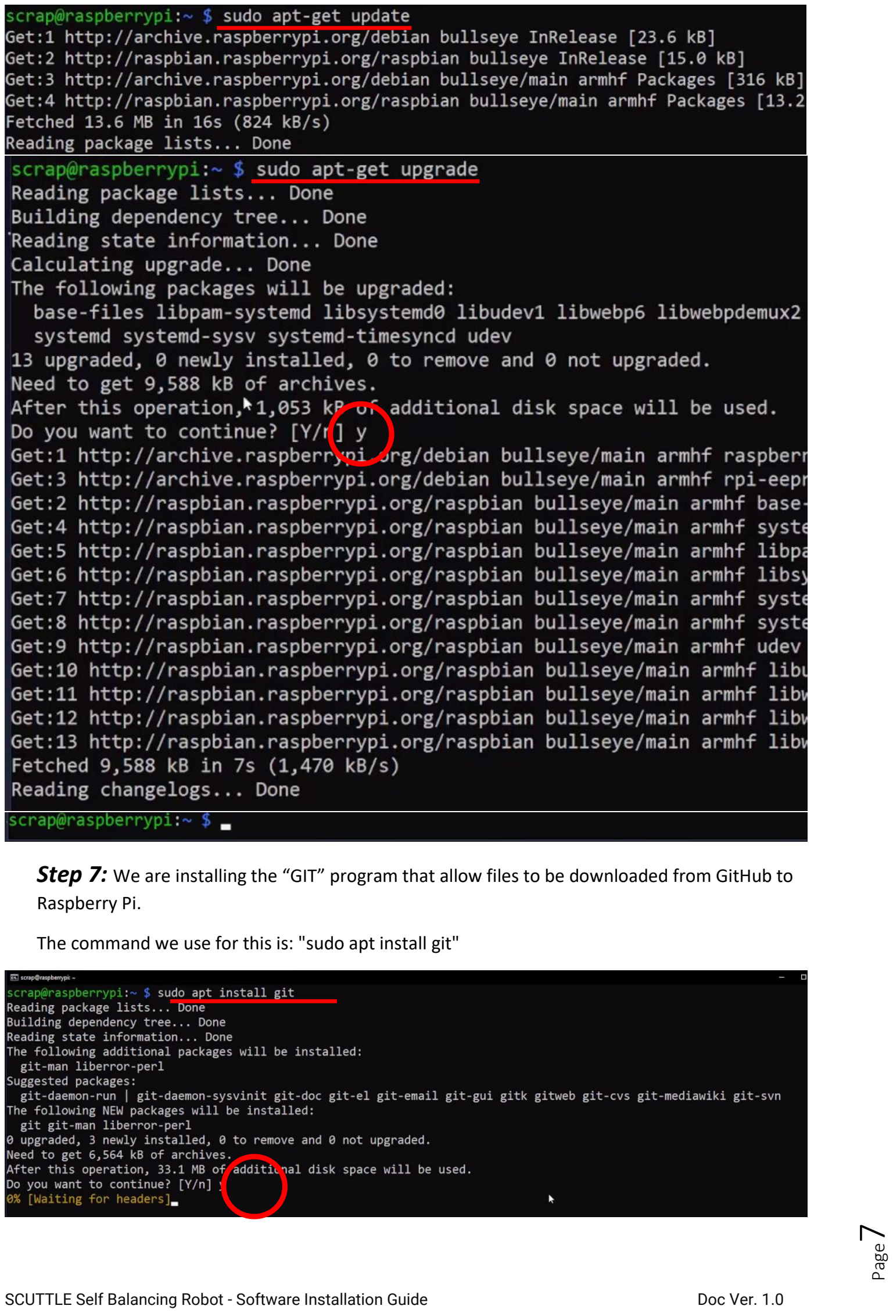
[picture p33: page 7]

Page

7

Step 7: We are installing the “GIT” program that allow files to be downloaded from GitHub to Raspberry Pi.

The command we use for this is: "sudo apt install git"

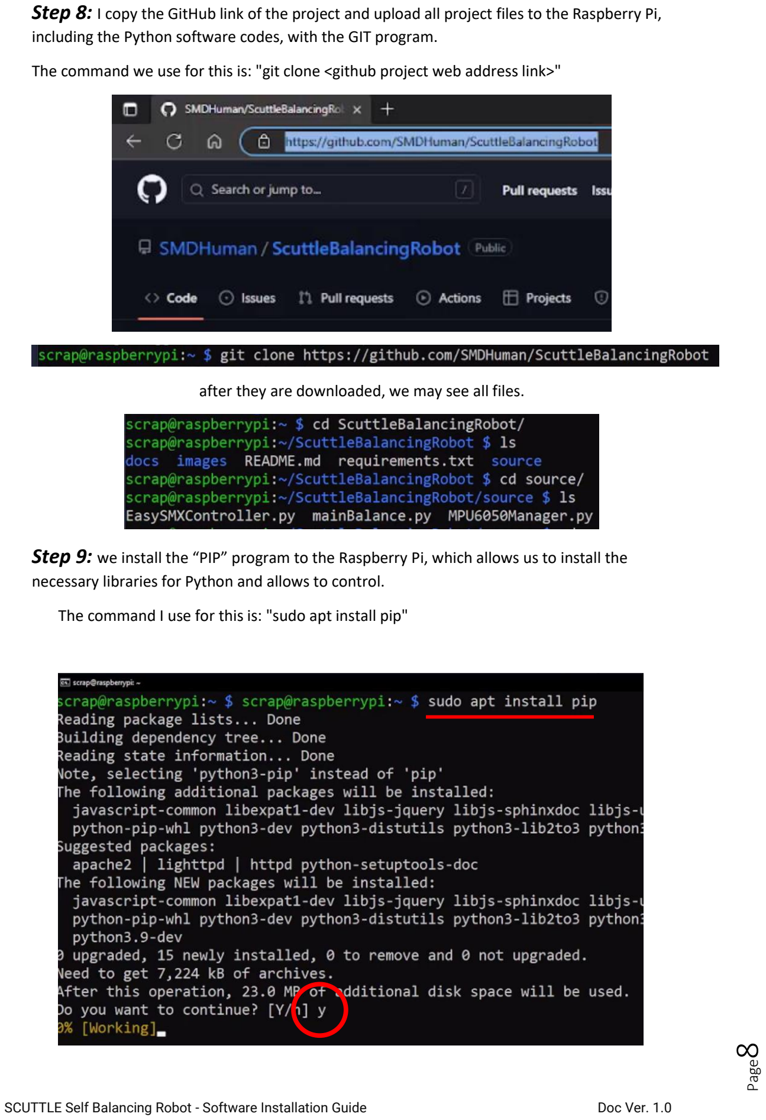
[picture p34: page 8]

Page

8

Step 8: I copy the GitHub link of the project and upload all project files to the Raspberry Pi, including the Python software codes, with the GIT program.

The command we use for this is: "git clone <github project web address link>"

after they are downloaded, we may see all files.

Step 9: we install the “PIP” program to the Raspberry Pi, which allows us to install the necessary libraries for Python and allows to control.

The command I use for this is: "sudo apt install pip"

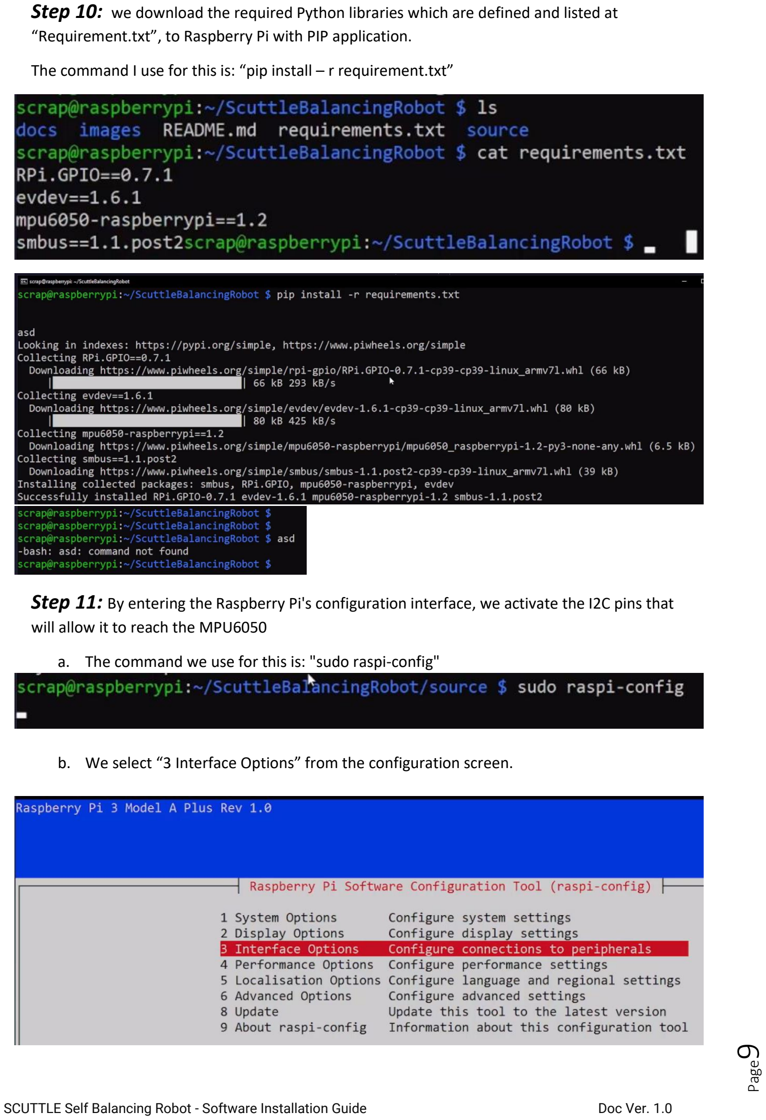
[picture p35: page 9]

Page

9

Step 10: we download the required Python libraries which are defined and listed at “Requirement.txt”, to Raspberry Pi with PIP application.

The command I use for this is: “pip install – r requirement.txt”

Step 11: By entering the Raspberry Pi's configuration interface, we activate the I2C pins that will allow it to reach the MPU6050
a. The command we use for this is: "sudo raspi-config"
b. We select “3 Interface Options” from the configuration screen.

Page10

c. Here we select “I5 I2C Enable/disable”.


d. we press the "Yes" button to enable the "ARM I2C interface".

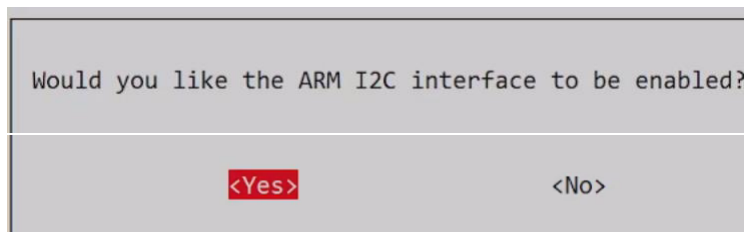
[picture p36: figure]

e. “ARM I2C” is enabled.

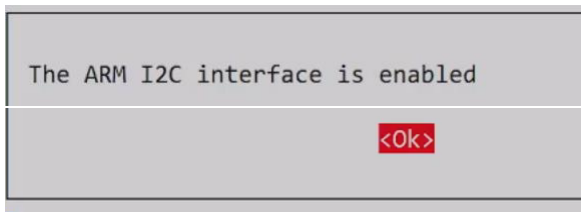
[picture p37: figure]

Step 12: we run the “mainBalance.py” Python software file. And the Balance Program starts to work. The command we use for this is: “python mainBalance.py”
Step 13: Problem 1: Here I am explaining the solution of the problem if you do not have the "Dongle" that allows us to communicate with the remote. I also explain how to see the name of the remote controller when it is found by the Raspberry Pi and how to update the code for that name.
a. First, we remove the "Dongle" from our robot.
b. We open the “mainBalance.py” file by using the “nano mainBalance.py” command.


Page11

c. Here Controller is seen as "event0".

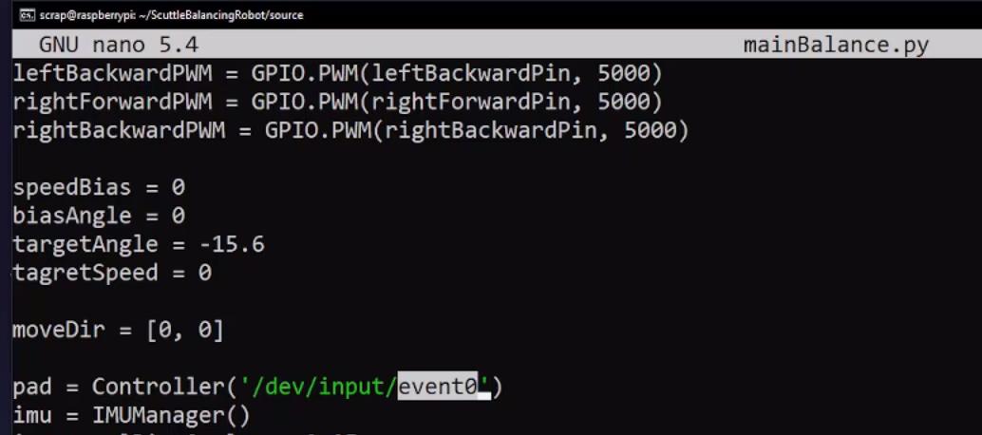
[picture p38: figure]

d. Only "event0" can be seen with the command "ls /dev/input".
e. we plug the "dongle" back into the Raspberry Pi.
f. When we check with the "ls /dev/input" command, we can see that the new control controller has been added to the system as "event1".
g. When this line is corrected in the "mainBalance.py" file in this way, the Controller will be seen by the system. "pad = Controller ('/dev/input/event1')"
Step 14: My robot works without any problem.

Page12

Step 15: Problem 2: In case of a problem with the brand of the controller, this code file should be modified accordingly.

Necessary adjustments are made in the “EasySMXController.py” file and a new different brand controller can be introduced to the system.

Step 16: If we want to disable the remote controller, these are the modifications needs to be done in the code here.
a. Firstly . We open the “mainBalance.py” file with the “nano mainBalance.py” command.
b. We put "#" at the beginning of the line “from EasySMXConroller import Controller” to disable the line

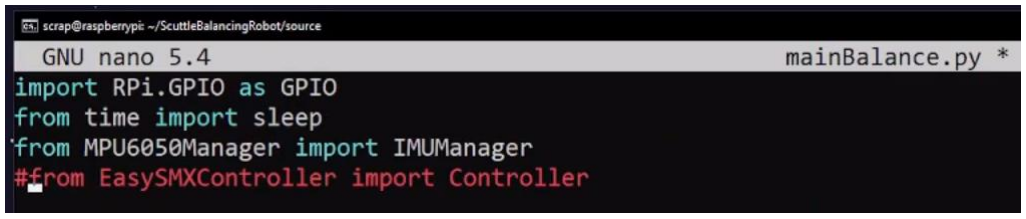
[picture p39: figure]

c. We put "#" at the beginning of ”pad= Controller('/dev/input/event1')'” line to disable it.
d. We assign 0 to the variables "speedPID.target" and "moveDir[1]"
Step 17: We can make our robot move at constant speed or stands still, by doing these changes in the code as it is given below.

"speedPID.target" is a variable where we control the speed of the robot. If we set a value of 0 to this variable, the robot stands still and does not move.

Step 18: We can make our robot to turn to the right or to the left, or make it stands still without turning, by doing these changes in the code as it is given below.

"speedPID.target" is a variable where I control the robot's right and left turns. If I assign a value of 0 to this variable, the robot stays in place and does not turn left or right.

Page13

Step 19: We can do the PID tuning in the code as follows.

When we need to fine tune the PID values, we can find the most successful values by changing the values of the p,i,d and sp,si,sd variables.

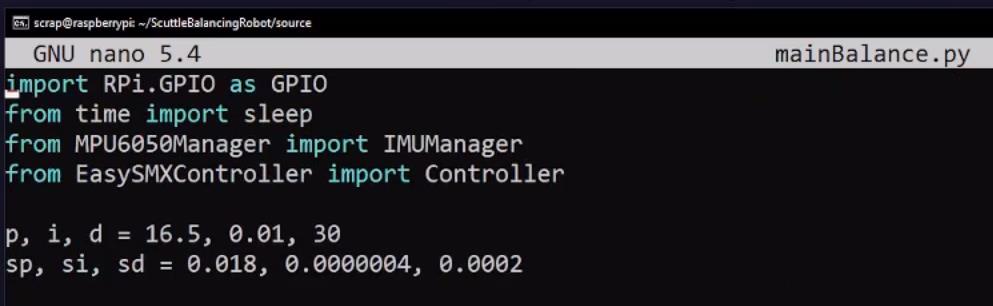
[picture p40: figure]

Step 20: Congratulations. Now you can keep your SCUTTLE robot balanced on two wheels. I would like to keep this document up to date with your suggestions. Please send the deficiencies you see or the areas that need improvement to my e-mail address reductalimenitis@gmail.com , I will definitely work on them. Enjoy.

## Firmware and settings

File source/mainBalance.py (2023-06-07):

import RPi.GPIO as GPIO
from time import sleep
from MPU6050Manager import IMUManager
from EasySMXController import Controller

p, i, d = 16.5, 0.01, 30
sp, si, sd = 0.018, 0.0000004, 0.0002

class PID():
    def __init__(self, p, i, d, target, minOut, maxOut):
        self.targetBias = 0
        self.target = target
        self.pK = p
        self.iK = i
        self.dK = d
        self.error = 0
        self.sumError = 0
        self.lastError = 0
        self.minOut = minOut
        self.maxOut = maxOut

    def update(self, now):
        self.error = (self.target + self.targetBias) - now
        self.sumError += self.error
        out = (self.error * self.pK) + (self.sumError * self.iK) + ((self.error - self.lastError) * self.dK)
        self.lastError = self.error

        out = self.minOut if out < self.minOut else out
        out = self.maxOut if out > self.maxOut else out
        return(out)

def setLeftMotor(x):
    if(x==0):
        leftBackwardPWM.stop()
        leftForwardPWM.stop()
    elif(x > 0):
        leftForwardPWM.start(min(x, 100))
        leftBackwardPWM.stop()
    elif(x < 0):
        leftBackwardPWM.start(-max(x, -100))
        leftForwardPWM.stop()

def setRightMotor(x):
    if(x==0):
        rightForwardPWM.stop()
        rightBackwardPWM.stop()
    elif(x > 0):
        rightForwardPWM.start(min(x, 100))
        rightBackwardPWM.stop()
    elif(x < 0):
        rightBackwardPWM.start(-max(x, -100))
        rightForwardPWM.stop()

leftForwardPin = 18
leftBackwardPin = 17
rightForwardPin = 23
rightBackwardPin = 22

GPIO.setmode(GPIO.BCM)

GPIO.setup(leftForwardPin, GPIO.OUT)
GPIO.setup(leftBackwardPin, GPIO.OUT)
GPIO.setup(rightForwardPin, GPIO.OUT)
GPIO.setup(rightBackwardPin, GPIO.OUT)

leftForwardPWM = GPIO.PWM(leftForwardPin, 5000)
leftBackwardPWM = GPIO.PWM(leftBackwardPin, 5000)
rightForwardPWM = GPIO.PWM(rightForwardPin, 5000)
rightBackwardPWM = GPIO.PWM(rightBackwardPin, 5000)

speedBias = 0
biasAngle = 0
targetAngle = -15.6
tagretSpeed = 0

moveDir = [0, 0]

pad = Controller('/dev/input/event0')
imu = IMUManager()
imu.accelBiasScaler = 0.05
gyroPID = PID(p, i, d, targetAngle, -100, 100)

speedPID = PID(sp, si, sd, tagretSpeed, -12, 12)

filteredAngles = imu.angles.copy()
f = 0.5
while(1):
	filteredAngles[1] = (imu.angles[1] * (1 - f)) + filteredAngles[1] * f

	speedPID.target = (pad.leftJoyY-128) * 40 / 128
	moveDir[1] = (pad.leftJoyX - 128) * 50 / 128

	gyroPID.targetBias = -speedPID.update(moveDir[0]) + speedBias
	moveDir[0] = gyroPID.update(filteredAngles[1])

	setLeftMotor(moveDir[0] + moveDir[1])
	setRightMotor(moveDir[0] - moveDir[1])
	#print(gyroPID.targetBias)
	#print(imu.angles[1], moveDir[0])
	#sleep(0.2)

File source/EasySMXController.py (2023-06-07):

from evdev import InputDevice, categorize, ecodes
import threading

class Code():
    # Type 3
    Xdpad = 16
    Ydpad = 17

    rightJoyX = 2
    rightJoyY = 5
    leftJoyX = 0
    leftJoyY = 1

    # Type 1
    a = 306
    b = 305
    x = 307
    y = 304

    start = 313
    back = 312

    rb = 309
    rt = 311
    lb = 308
    lt = 310

class Controller():
    def __init__(self, port):
        self.gamepad = InputDevice(port)
        
        self.rightJoyX = 128
        self.rightJoyY = 128
        self.leftJoyX = 128
        self.leftJoyY = 128
        
        self.right = 0
        self.left = 0
        self.up = 0
        self.down = 0
        
        
        self.a = 0
        self.b = 0
        self.x = 0
        self.y = 0

        self.start = 0
        self.back = 0

        self.rb = 0
        self.rt = 0
        self.lb = 0
        self.lt = 0
        
        a = threading.Thread(target = self.gamepadLoop, args = ())
        a.start()
        
    def gamepadLoop(self):
        for event in self.gamepad.async_read_loop():
            if(event.type == 1):
                if(event.code == Code.a):
                        self.a = event.value
                if(event.code == Code.b):
                        self.b = event.value
                if(event.code == Code.x):
                        self.x = event.value
                if(event.code == Code.y):
                        self.y = event.value
                if(event.code == Code.start):
                        self.start = event.value
                if(event.code == Code.back):
                        self.back = event.value
                if(event.code == Code.rb):
                        self.rb = event.value
                if(event.code == Code.rt):
                        self.rt = event.value
                if(event.code == Code.lb):
                        self.lb = event.value
                if(event.code == Code.lt):
                        self.lt = event.value
            if(event.type == 3):
                if(event.code == Code.rightJoyX):
                        self.rightJoyX = event.value
                if(event.code == Code.rightJoyY):
                        self.rightJoyY = event.value
                if(event.code == Code.leftJoyX):
                        self.leftJoyX = event.value
                if(event.code == Code.leftJoyY):
                        self.leftJoyY = event.value
                    
                if(event.code == Code.Xdpad):
                        if(event.value == 1):
                            self.right = 1
                        elif(event.value == -1):
                            self.left = 1
                        else:
                            self.right = 0
                            self.left = 0
                if(event.code == Code.Ydpad):
                        if(event.value == -1):
                            self.up = 1
                        elif(event.value == 1):
                            self.down = 1
                        else:
                            self.down = 0
                            self.up = 0


if(__name__ == "__main__"):
    
    import time
    c = Controller('/dev/input/event0')
    while(1):
        print(c.lt, c.rt, c.lb, c.rb)
        print(c.back, c.start)
        print(c.a, c.b, c.x, c.y)
        print(c.rightJoyX, c.rightJoyY, c.leftJoyX, c.leftJoyY)
        print(c.right, c.left, c.up, c.down)
        
        print()
        time.sleep(0.2)
    
